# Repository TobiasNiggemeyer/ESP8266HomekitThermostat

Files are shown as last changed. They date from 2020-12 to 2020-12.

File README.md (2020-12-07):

# ESP8266HomekitThermostat

This project is used to modify the "Eqiva Thermostat Model N, 132231K0A" to enable Apple Homekit using an ESP8266-01.
The source code is based on Mixiaoxio Arduino-HomeKit-ESP8266 project (see https://github.com/Mixiaoxiao/Arduino-HomeKit-ESP8266).
The GPIOs 0 and 2 of the esp are connected to the rotary encoder of the thermostat to automate the function (see https://www.youtube.com/watch?v=m0ZxRcsp5y4). To use this extension for the thermostat, connect the two outputs of the rotary encoder to T1 and T2 of the PCB and the GND pin of the rotary encoder to GND of the PCB (see images). Moreover, the voltage level of the outputs of the rotary encoder must be high since the system pulls the signals to GND (turn rotary encoder once -> check if the system works -> if not turn again). 

The project includes the following parts:
  - ESP8266 source code
  - 3d model to interate the ESP into the thermostat (not perfect but works)
  - schematic and layout
  
## Components/Costs
  - Eqiva Thermostat Model N, 132231K0A   ~ 10,00€
  - 2x NPN-transistor:                    ~ 0,700€
  - 4x 1k resistor:                       ~ 0,070€
  - 2x 10k resistor:                      ~ 0,035€
  - 1x xx-xx stripe grid board:           ~ 0,500€
  - 1x esp8266-01:                        ~ 3,000€
  - 1x 5V-3.3V regulator:                 ~ 0.700€
  - some wires                            -
### Sum:                                  ~ 15,00€
  
## Images
 <div class="row">
  <div class="column">
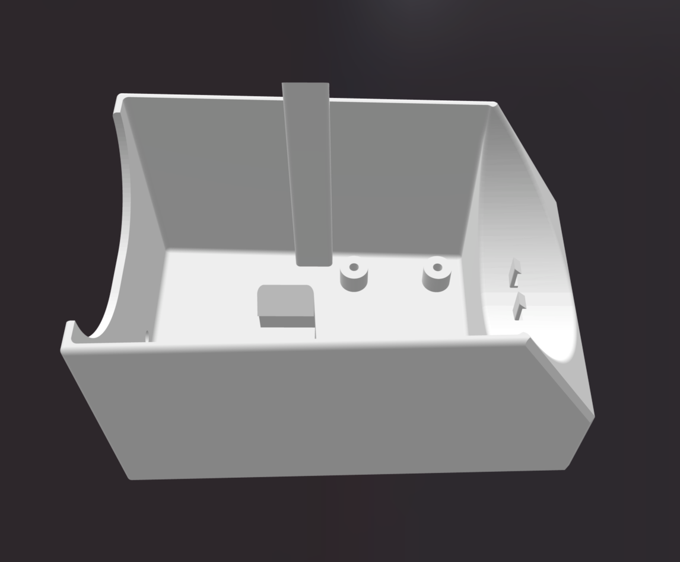
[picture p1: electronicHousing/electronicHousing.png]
    
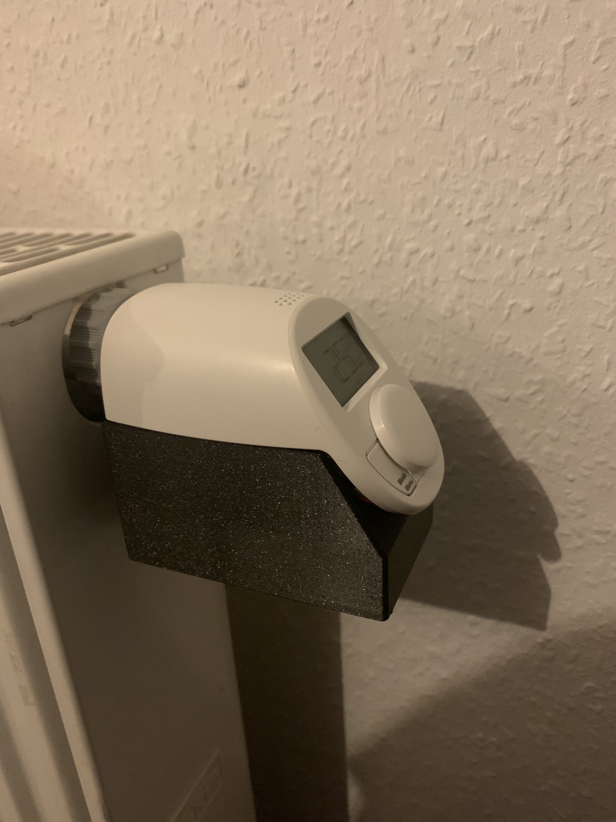
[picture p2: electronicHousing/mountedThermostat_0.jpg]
    
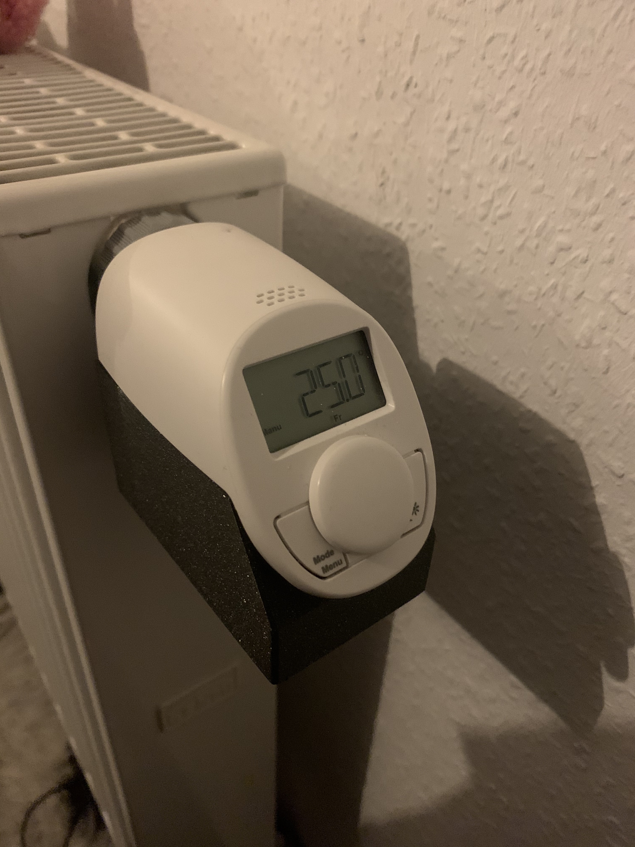
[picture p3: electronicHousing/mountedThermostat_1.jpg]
    
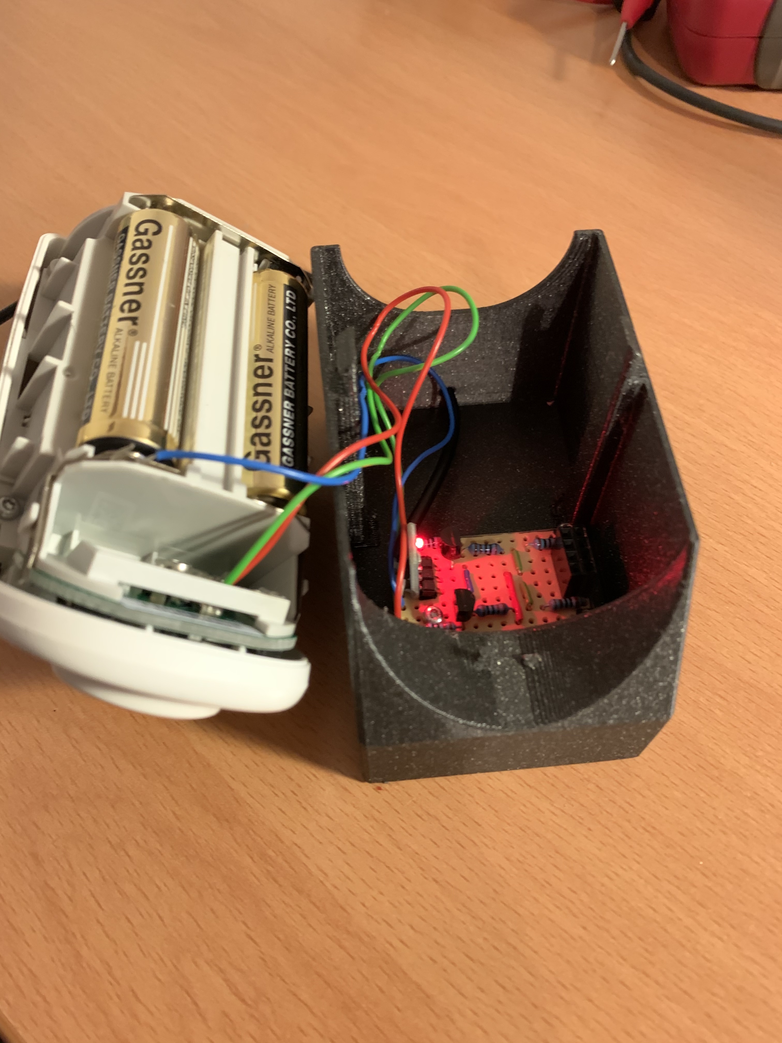
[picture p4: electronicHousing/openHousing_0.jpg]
    
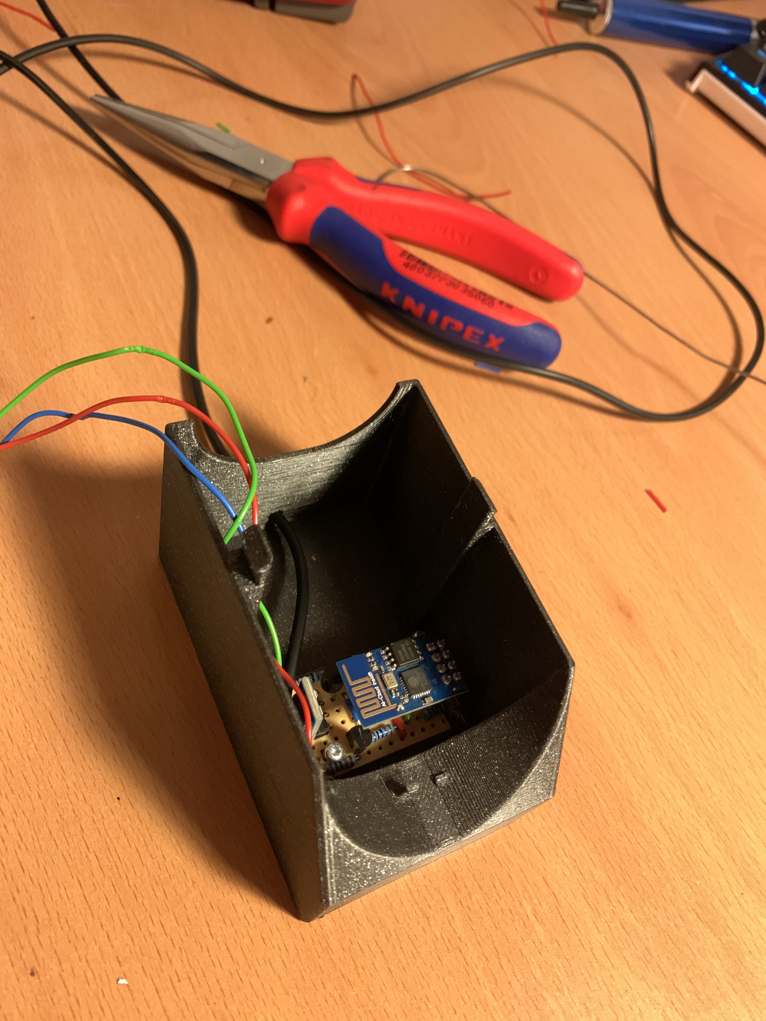
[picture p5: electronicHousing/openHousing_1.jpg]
    
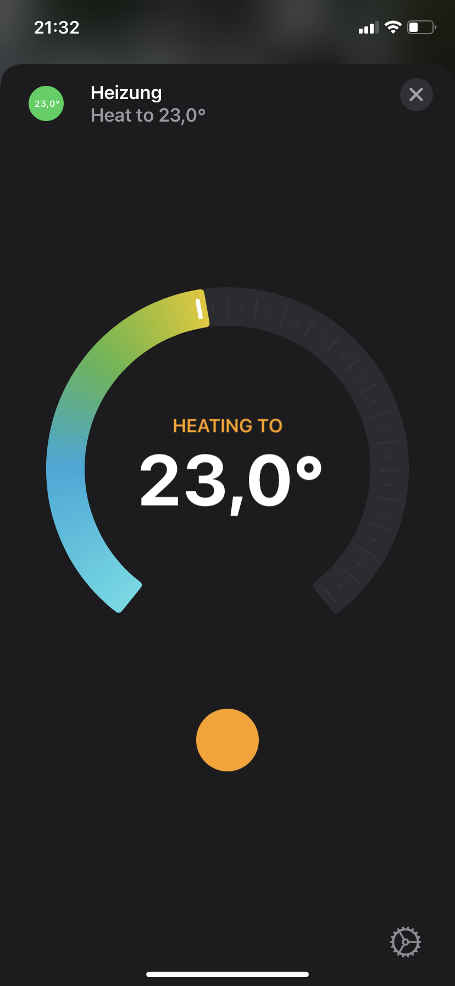
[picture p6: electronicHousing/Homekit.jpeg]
    
  </div>
</div> 

## Schematics
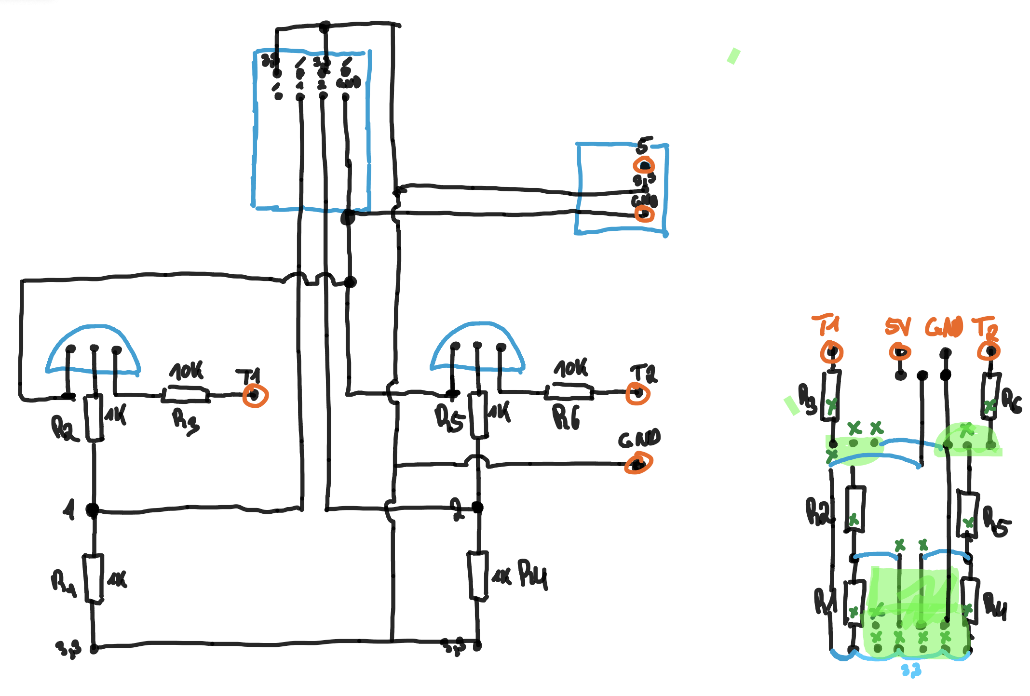
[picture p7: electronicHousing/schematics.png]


### Hint: 
R1 and R4 are used to pull the GPIOs of the ESP to a floating level of around 1V to enable the direct boot of the esp (esp enters different modes if one or both GPIOs are pulled to GND).

## Instructions

- change SSID and password in wifi_info.h
- compile and flash software to esp8266-01
  - power the esp: 3.3V to pin 8 and 4, GND to pin 1
  - connect usb to seral converter: TX->RX(7), RX->TX(2), GND->GNC(1)
  - pull GPIO-0(5) to GND (use 10k resistor)
  - reset esp by connection Reset(6) to GND
  - disconnect GPIO-0(5) and Reset(6) from ground
  - compile and flash esp8266-01 using the arduino IDE
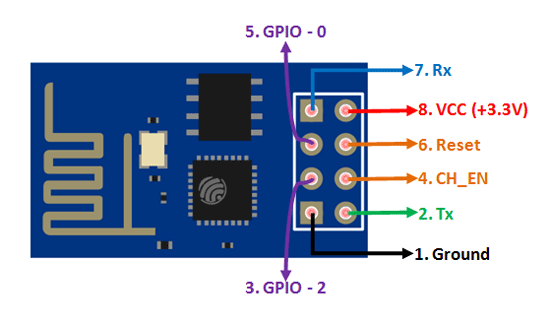
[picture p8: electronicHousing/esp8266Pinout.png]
 

## Open Points

- Improve housing for the electronics
  - smaller
  - better fit
- removal of power supply by battery 
- create detailed/professional schematics
- add an LED to indicate if the signal of the rotary encoder is high (needed to simulate the rotary encoder with the esp)

### Feel free to ask questions and improve the thermostat

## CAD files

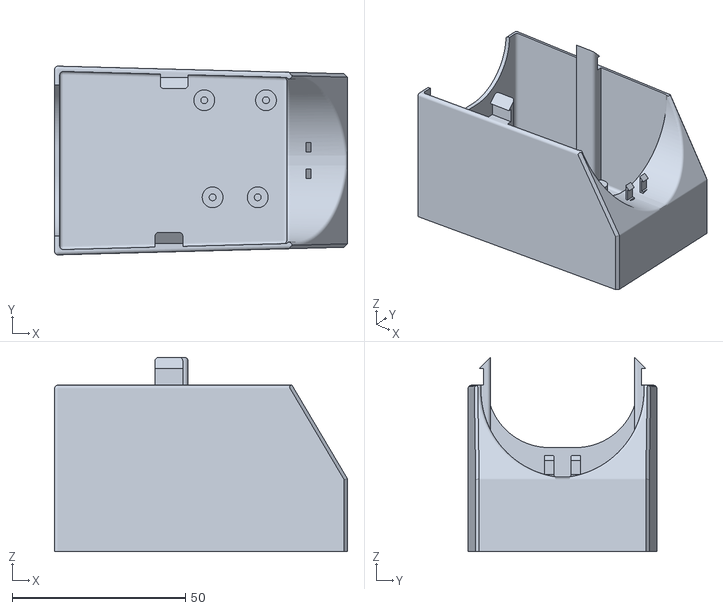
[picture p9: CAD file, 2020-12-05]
electronicHousing/electronicHousing.stl
84.5 x 54.4 x 56.0

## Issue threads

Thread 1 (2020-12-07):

Questions: How long doe the batteries last

maccoylton, 2020-12-07:
I'm curious as to how long the batteries last?

TobiasNiggemeyer, 2020-12-07:
The "addon" is currently powered by a 5V DC Adapter (see README section open points). In my case this is a suitable solution, but it would be nice to add a battery to the system (maybe i have to change the mainboard, since the esp8266-01 draws alot of current)

Closed 2020-12-14.

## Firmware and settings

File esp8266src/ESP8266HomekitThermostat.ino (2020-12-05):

/*
 * Example05_WS2812_Neopixel.ino
 *
 *  Created on: 2020-10-01
 *      Author: Juergen Fink
 *	Thanks to all the other helpful people commenting here.
 *
 * This example allows to change brightness and color of a connected neopixel strip/matrix
 *
 * You should:
 * 1. read and use the Example01_TemperatureSensor with detailed comments
 *    to know the basic concept and usage of this library before other examples。
 * 2. erase the full flash or call homekit_storage_reset() in setup()
 *    to remove the previous HomeKit pairing storage and
 *    enable the pairing with the new accessory of this new HomeKit example.
 */


#include <Arduino.h>
#include <arduino_homekit_server.h>
#include "wifi_info.h"
#include <homekit/types.h>

#define LOG_D(fmt, ...)   printf_P(PSTR(fmt "\n") , ##__VA_ARGS__);
int gpioToThermo1 = 0;
int gpioToThermo2 = 2;
void setup() {
	Serial.begin(115200);
	wifi_connect(); // in wifi_info.h
  //homekit_storage_reset();
  delay(1000);
  pinMode(gpioToThermo1, OUTPUT);
  pinMode(gpioToThermo2, OUTPUT);
	my_homekit_setup();
}

void loop() {
	my_homekit_loop();
	delay(10);
}

//==============================
// HomeKit setup and loop
//==============================

// access your HomeKit characteristics defined in my_accessory.c

extern "C" homekit_server_config_t accessory_config;
extern "C" homekit_characteristic_t currState;
extern "C" homekit_characteristic_t reqState;
extern "C" homekit_characteristic_t currTemp;
extern "C" homekit_characteristic_t reqTemp;
extern "C" homekit_characteristic_t unitDisp;
extern "C" uint8_t returnState;
extern "C" float returnTemp;

static uint32_t next_heap_millis = 0;
bool sendTempToHomekitDevice = FALSE;

void my_homekit_setup() {
  reqState.setter = setState;               // setter function, which is called if the apple decive changes the state
  reqTemp.setter  = setTemp;                // setter function, which is called if the apple device changes the temperature
  unitDisp.setter = setDispUnit;            // setter function, which is called if the apple device changes the display unit  
	arduino_homekit_setup(&accessory_config); // lets create the apple homekit accessory
}

int  gradToZero    = 35;    // since we need to set the thermostat to zero (no feedback) we need the max value of the thermostat
bool setThermoTemp = FALSE; // Flag which is used to set the temperature in main loop
int  setZeroState  = 0;     // different states, which include the state of each GPIO
bool setThermoZero = FALSE; // Flag which is used to set the temperature to zero in main loop
int  setZeroCnt    = 0;     // count how much celsius are decreased 
int  setTempState  = 0;     // different states, which include the state of each GPIO
int  setTempCnt    = 0;     // count how much ceksius are increased
float targetTemp   = 10;     // requested target temperature send by the apple device
float lastSetTemp  = 10;     // remember the last set value
int   delaySwtTimeSetThermo   = 10; // difference time between rising and falling edges: 10 ms
int   delayOnTimeSetThermo    = 50; // time the GPIO stays on and off: 50 ms
static uint32_t nextSetThermo = 0;  // time which triggers the next state change of the GPIO



// main loop for homekit device
void my_homekit_loop() {
	arduino_homekit_loop();
	const uint32_t t = millis();
	if (t > next_heap_millis) { 
		// show heap info every 5 seconds
		next_heap_millis = t + 5 * 1000;
		LOG_D("Free heap: %d, HomeKit clients: %d",ESP.getFreeHeap(), arduino_homekit_connected_clients_count());
    if(sendTempToHomekitDevice == TRUE){
      //float temperature_value = random_value(10, 30); // FIXME, read your real sensor here.
      currTemp.value.float_value = targetTemp;
      homekit_characteristic_notify(&currTemp, currTemp.value);      
    }
	}
  // set the thermostat if needed
  if(t > nextSetThermo){
    if(setThermoTemp){
      if(setThermoZero){
        switch(setZeroState){
          case 0:
            nextSetThermo = t + delaySwtTimeSetThermo;
            digitalWrite(gpioToThermo1,LOW);
            setZeroState = 1;
          break;
          case 1:
            nextSetThermo = t + delayOnTimeSetThermo;
            digitalWrite(gpioToThermo2,LOW);
            setZeroState = 2;
          break;
          case 2:
            nextSetThermo = t + delaySwtTimeSetThermo;
            digitalWrite(gpioToThermo1,HIGH);
            setZeroState = 3;
          break;
          case 3:
            nextSetThermo = t + delayOnTimeSetThermo;
            digitalWrite(gpioToThermo2,HIGH);
            setZeroState = 0;
          break;
          }
          setZeroCnt = setZeroCnt + 1;
          if(setZeroCnt >= gradToZero*4){
            Serial.print("setZeroCnt: ");
            Serial.println(setZeroCnt);
            Serial.print("setZeroState: ");
            Serial.println(setZeroState);
            setZeroCnt = 0;
            setTempCnt = 0;
            setThermoZero = FALSE;
          }
      }
      else if(!setThermoZero && returnState != 0){
        switch(setTempState){
          case 0:
            nextSetThermo = t + delaySwtTimeSetThermo;
            digitalWrite(gpioToThermo2,LOW);
            setTempState = 1;
          break;
          case 1:
            nextSetThermo = t + delayOnTimeSetThermo;
            digitalWrite(gpioToThermo1,LOW);
            setTempState = 2;
          break;
          case 2:
            nextSetThermo = t + delaySwtTimeSetThermo;
            digitalWrite(gpioToThermo2,HIGH);
            setTempState = 3;
          break;
          case 3:
            nextSetThermo = t + delayOnTimeSetThermo;
            digitalWrite(gpioToThermo1,HIGH);
            setTempState = 0;
          break;
          }
          setTempCnt = setTempCnt + 1;
          if(setTempCnt >= ((int)targetTemp-5)*4+2){
            Serial.print("setTempCnt: ");
            Serial.println(setTempCnt);
            Serial.print("setTempState: ");
            Serial.println(setTempState);
            setTempCnt = 0;
            setZeroCnt = 0;
	    setTempState = 0;
            setThermoZero = TRUE;
            setThermoTemp = FALSE;
          }    
      }
      else{
          setThermoZero = TRUE;
          setThermoTemp = FALSE;        
      }
    }
    else{
      nextSetThermo = t + delayOnTimeSetThermo;
    }
    
  }
}

void setState(const homekit_value_t v) {
  Serial.println("setState");
  sendTempToHomekitDevice = TRUE;
  uint8_t state = v.int_value;
  returnState = state;
  reqState.value.int_value = state;
  if(state == 0){
    returnTemp = 10;
    targetTemp = 10;
    setThermoTemp = TRUE;
    setThermoZero = TRUE;
    reqTemp.value.float_value = 10;
  }
  else{
    returnTemp = lastSetTemp;
    targetTemp = lastSetTemp;
    setThermoTemp = TRUE;
    setThermoZero = TRUE;
    reqTemp.value.float_value = lastSetTemp;    
  }
}

void setTemp(const homekit_value_t v) {
  Serial.println("setTemp");
  float temp = v.float_value;
  returnTemp = temp;
  targetTemp = temp;
  lastSetTemp = temp;
  setThermoTemp = TRUE;
  setThermoZero = TRUE;
  reqTemp.value.float_value = temp;
}

void setDispUnit(const homekit_value_t v) {
  Serial.println("setDispUnit");
  uint8_t dispUnit = v.int_value;
  reqTemp.value.float_value = dispUnit;
}
